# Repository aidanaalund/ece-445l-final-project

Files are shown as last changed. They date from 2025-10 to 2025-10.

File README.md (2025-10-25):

# ECE 445L Final Project

This final project is titled 'Magic Wand'. The user's hand is tracked with a sensor and the fans in the tubes will make a ping pong ball float to match the user's hand distance. Won professor's vote at the Spring 2025 Embedded Systems competition.

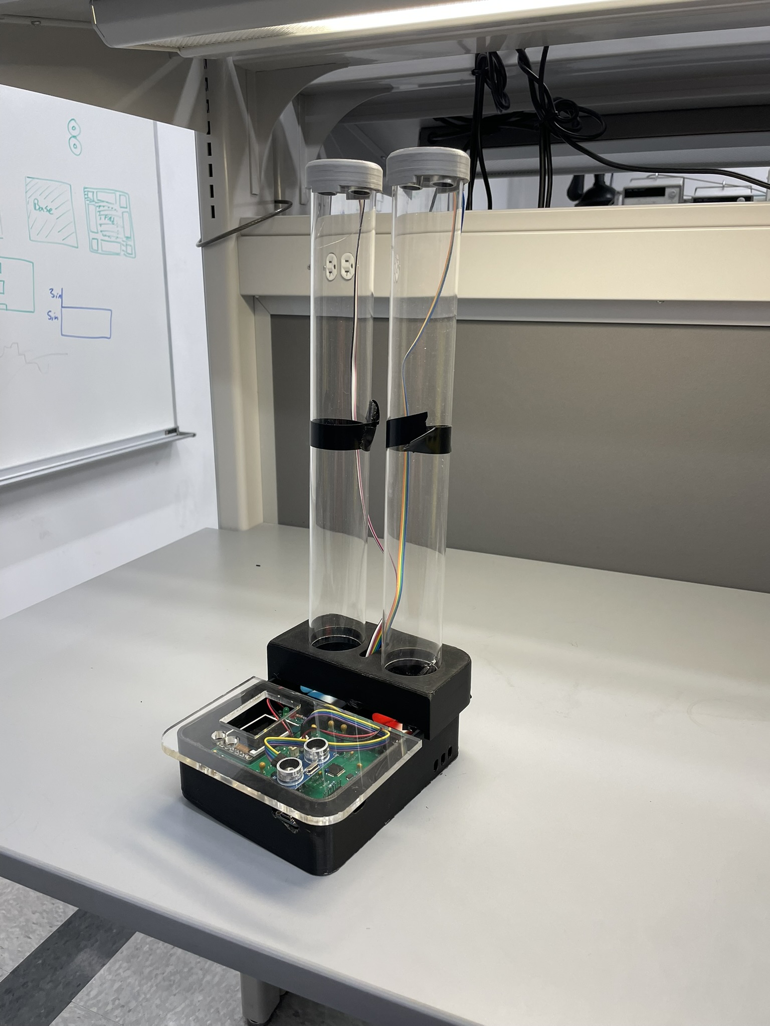
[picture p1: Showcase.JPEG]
Entire system including packaging and sensors connected
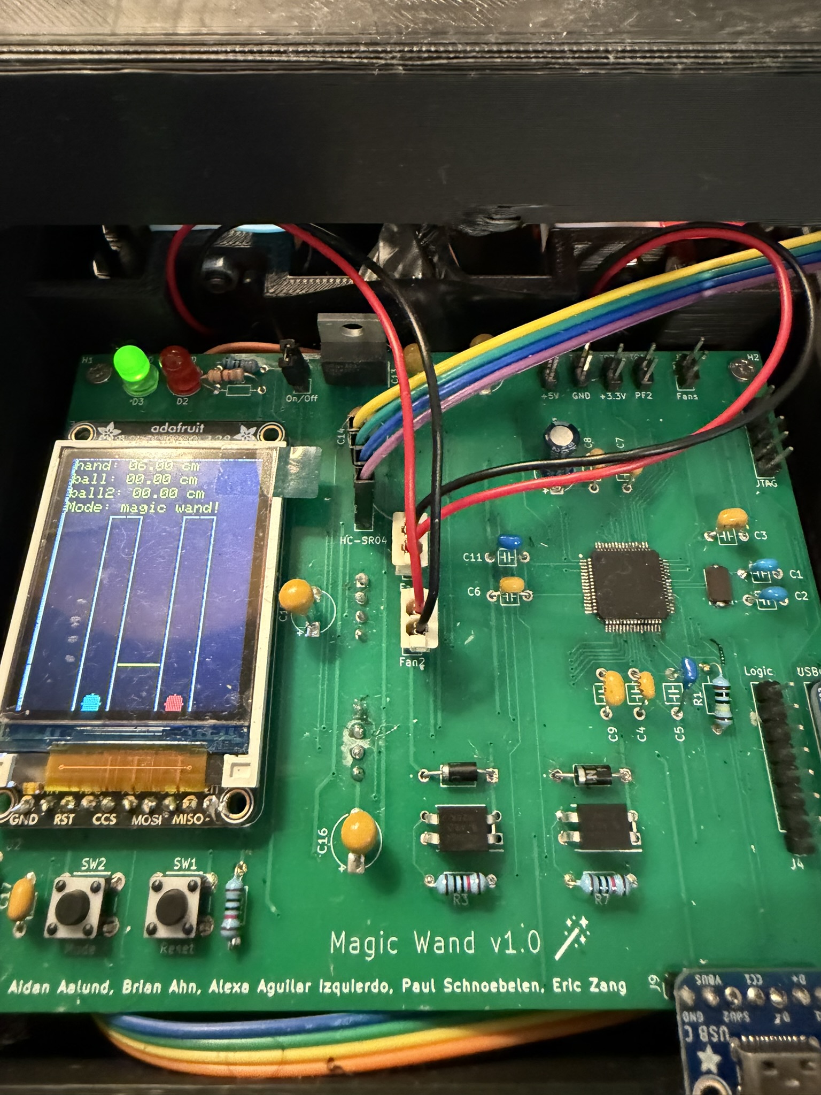
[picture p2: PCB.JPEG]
PCB featuring the TM4C microcontroller, all hand soldered.
 

## 0 Repository Structure

The typical explanation for the repo structure. Lab specific instructions can be
found further below.

### 0.1 HW

The `hw` folder should contain your schematic and board files for your PCB or
circuits. In labs 1-5 and 10, you will be creating schematics for your circuit
in KiCad. 

### 0.2 SW

The `sw` folder should contain your application firmware and software written
for the lab. The `sw/inc` folder contains firmware drivers written for you by
Professor Valvano. Feel free to write your own (in fact, in some labs, you may
be required to write your own).

You can place any other source files in the `sw` folder. TAs will look at the
files you create and/or modify for software quality and for running your
project.

### 0.3 Resources

A couple files are provided in the Resources folder so you don't have to keep
searching for that one TI document. Some of them are immediately useful, like
the TM4C datasheet. Others may be useful for your final project, like the
TM4C_System_Design_Guidelines page.

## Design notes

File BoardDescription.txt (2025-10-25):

Our board will help us create a fun visual effect with a tube, fan, and ping pong ball in the tube. 
The PCB will contain connections for 2 HC-SR40 Ultrasonic distance sensors and a motor that can be interfaced with PWM (circuit similar to Lab 2/3/4).
The user will use their hand (or a magic wand we give them) to point at a spot on the tube, read by one of the distance sensors.
Using a second distance sensor to read the ping pong ball's position, we will move the ping pong ball in the tube to match the other sensor's position with a PI loop.
This will give the appearance that the ball 'magically' follows the user's wand/hand.
There will also be additional modes for the user to switch between with an onboard pushbutton such as an off state, hover, and oscillate (hopefully!).

NOTE: the board will be powered by a USB-C 5V connection using this breakout board:
https://www.adafruit.com/product/4090

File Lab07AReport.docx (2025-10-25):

Name: __Aidan Aalund, Alexa Aguilar Izquierdo, Paul Schnoebelen, Eric Zang, Brian Ahn____

EID: __ ala4225, aa88886, pds2239, etz87, ba26422_____

Semester: Fall 2025

Course: ECE445L

A) Objectives:

1. In a few sentences, describe the purpose of the lab:

To learn about embedded system design, particularly when crafting the bill of materials and schematic of the embedded system.

B) Hardware Design Deliverables:

1. Deliverable 1: Using KiCad, create a schematic for your design. Include a screenshot in the space below.

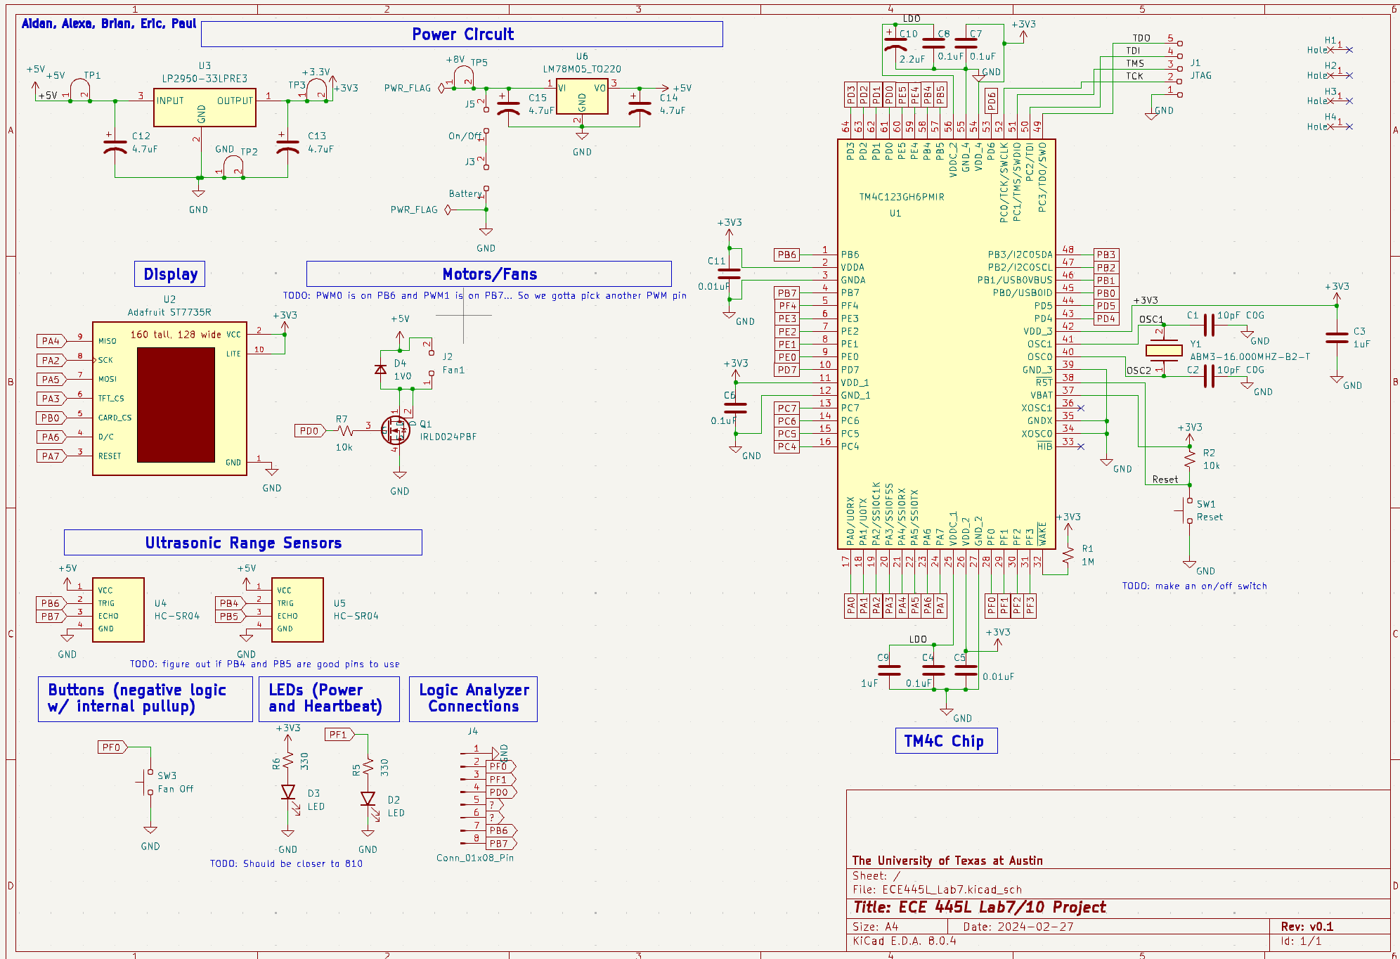
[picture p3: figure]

2. Deliverable 2: Using KiCad, create a Layout for your design. Include a screenshot in the space below.

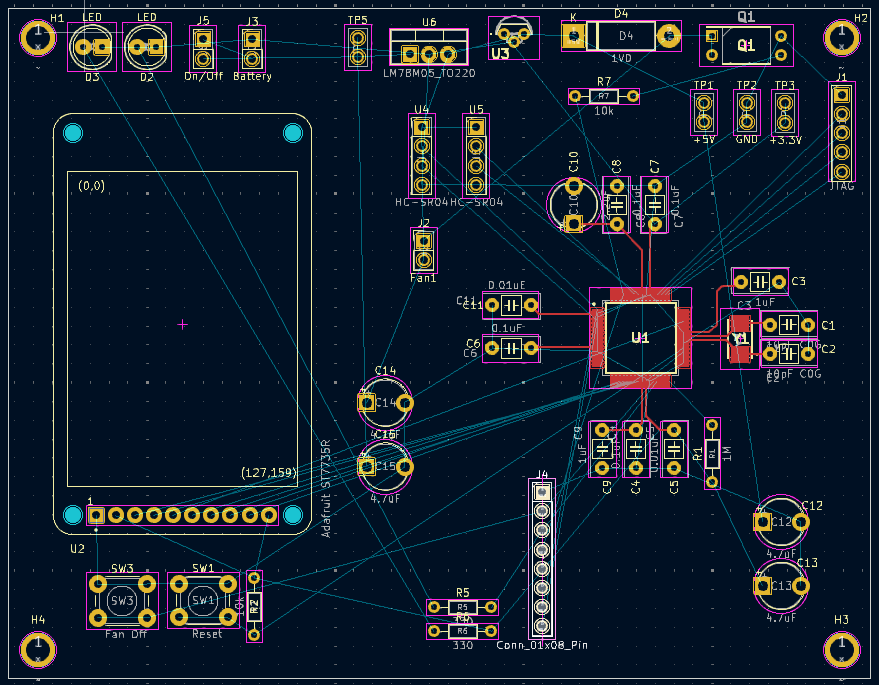
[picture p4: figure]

C) Software Design Deliverables:

I have pushed my project to GitHub for grading (Yes/No): Yes

1. Deliverable 3: System design diagram of the modules created.

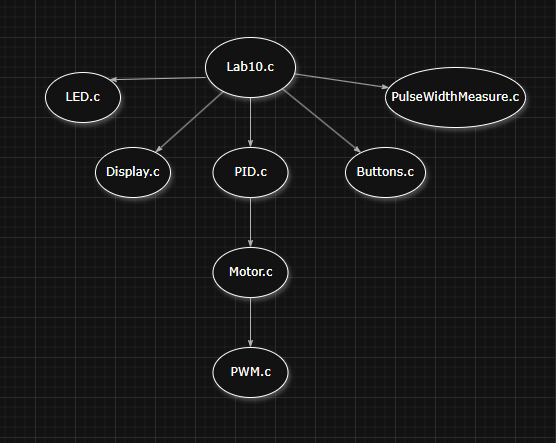
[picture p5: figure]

D) Deliverables:

1. Deliverable 4: Total cost estimate

I have updated the bill of materials (Yes/No): Yes

Out of pocket costs: $56.99

Adjusted competition costs: $42.44

2. Deliverable 5: Estimated current usage

TM4C: 45mA

Display: 50mA

Motors: 2(300mA)

Motion Sensor: 3(15mA)

Voltage Regulator: 100mA

LEDs: 2mA + 1mA

Total Current Usage: 45m + 2(300m) + 3(15m) + 100m + 2m + 1m + 50mA

= 0.843A

3. Deliverable 6 (5pt EC): TIW Training

Alexa got 3D printing training, Aidan is in progress.

4. Deliverable 7 (10pt EC): Discrete IC usage

Yes, check the layout.

5. Deliverable 8 (10pt EC): Characterization of the system

E) Analysis and Discussion Questions:

1. How did you debug your system? How intrusive was it?

We debugged our system through unit tests (‘test’ mains in each C file). In these unit tests we did a mix of intrusive breakpoint debugging and unintrusive functional debugging. For the PWM of the motor, we debugged the duty cycle and frequency with a logic analyzer (minimally intrusive). Once a module was unit tested, we performed integration tests by adding it to the Lab10.c main file and checking to see if behavior was the same as unit tests.

2. What’s the difference between unit testing, integration testing, and functional testing?

Unit testing is testing a single component of the system in isolation, whereas integration tests check if the module can function in the system with other components active. Functional testing is to see if the system works as per the requirements document.

Lab 7A report ECE445L

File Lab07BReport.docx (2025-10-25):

Name: __Aidan Aalund, Alexa Aguilar Izquierdo, Paul Schnoebelen, Eric Zang, Brian Ahn____

EID: __ ala4225, aa88886, pds2239, etz87, ba26422_____

Semester: Fall 2024

Course: ECE445L

A) Objectives:

1. In a few sentences, describe the purpose of the lab.

The purpose of this lab is to learn about the layout of an embedded system in the context of embedded system design. Examples include placement of bypass capacitors, routing power/digital/analog signals, and use of integrated circuits.

B) Hardware Design Deliverables:

1. Deliverable 1: Using KiCad, create a schematic for your design. Include a screenshot in the space below.

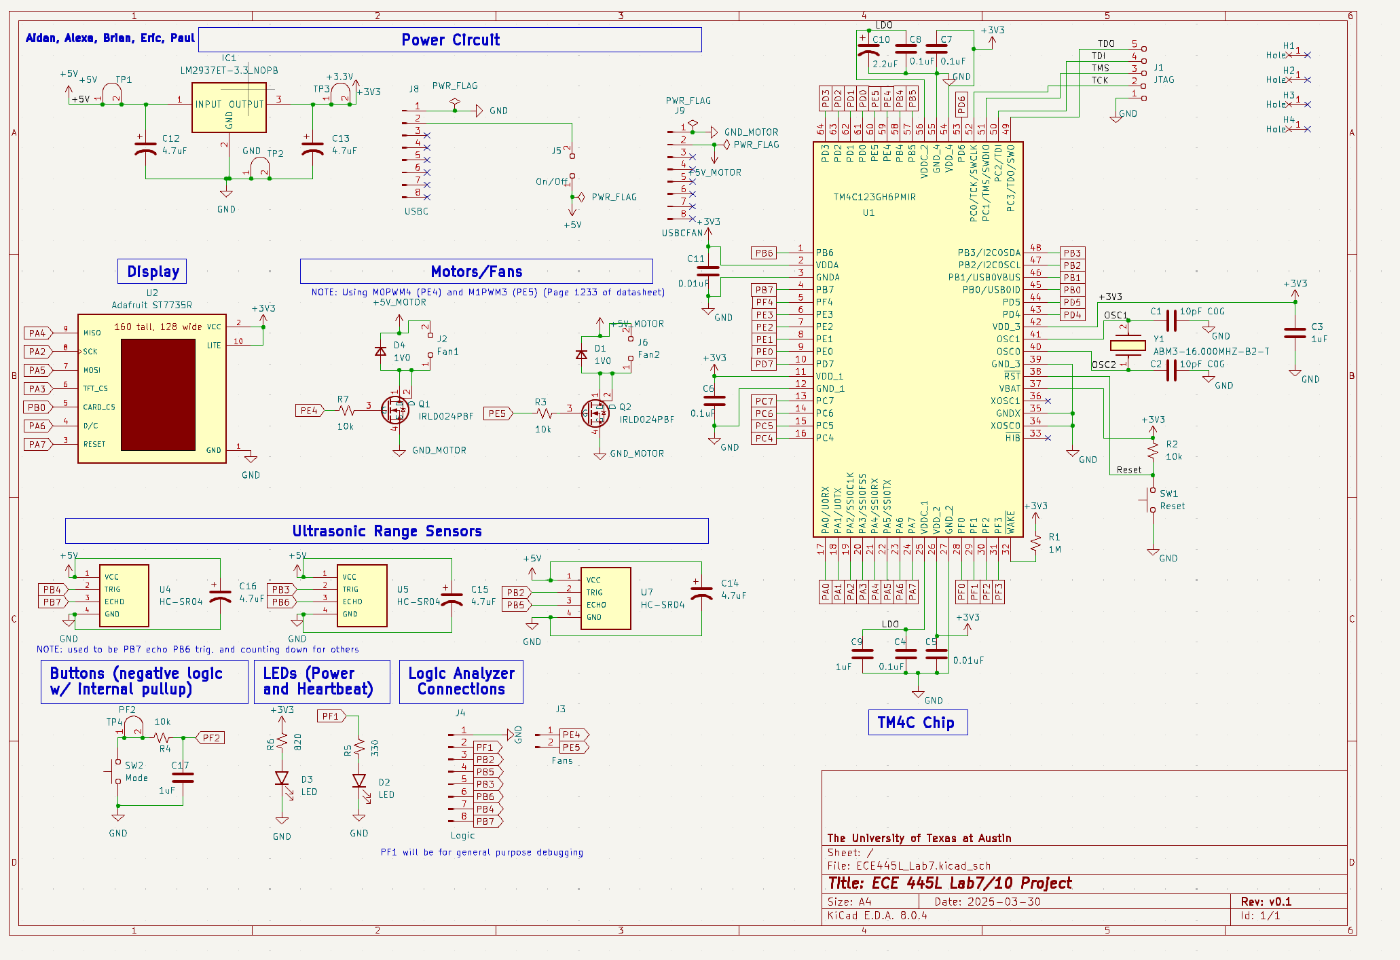
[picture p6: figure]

2. Deliverable 2: Using KiCad, create a Layout for your design. Include a screenshot in the space below.

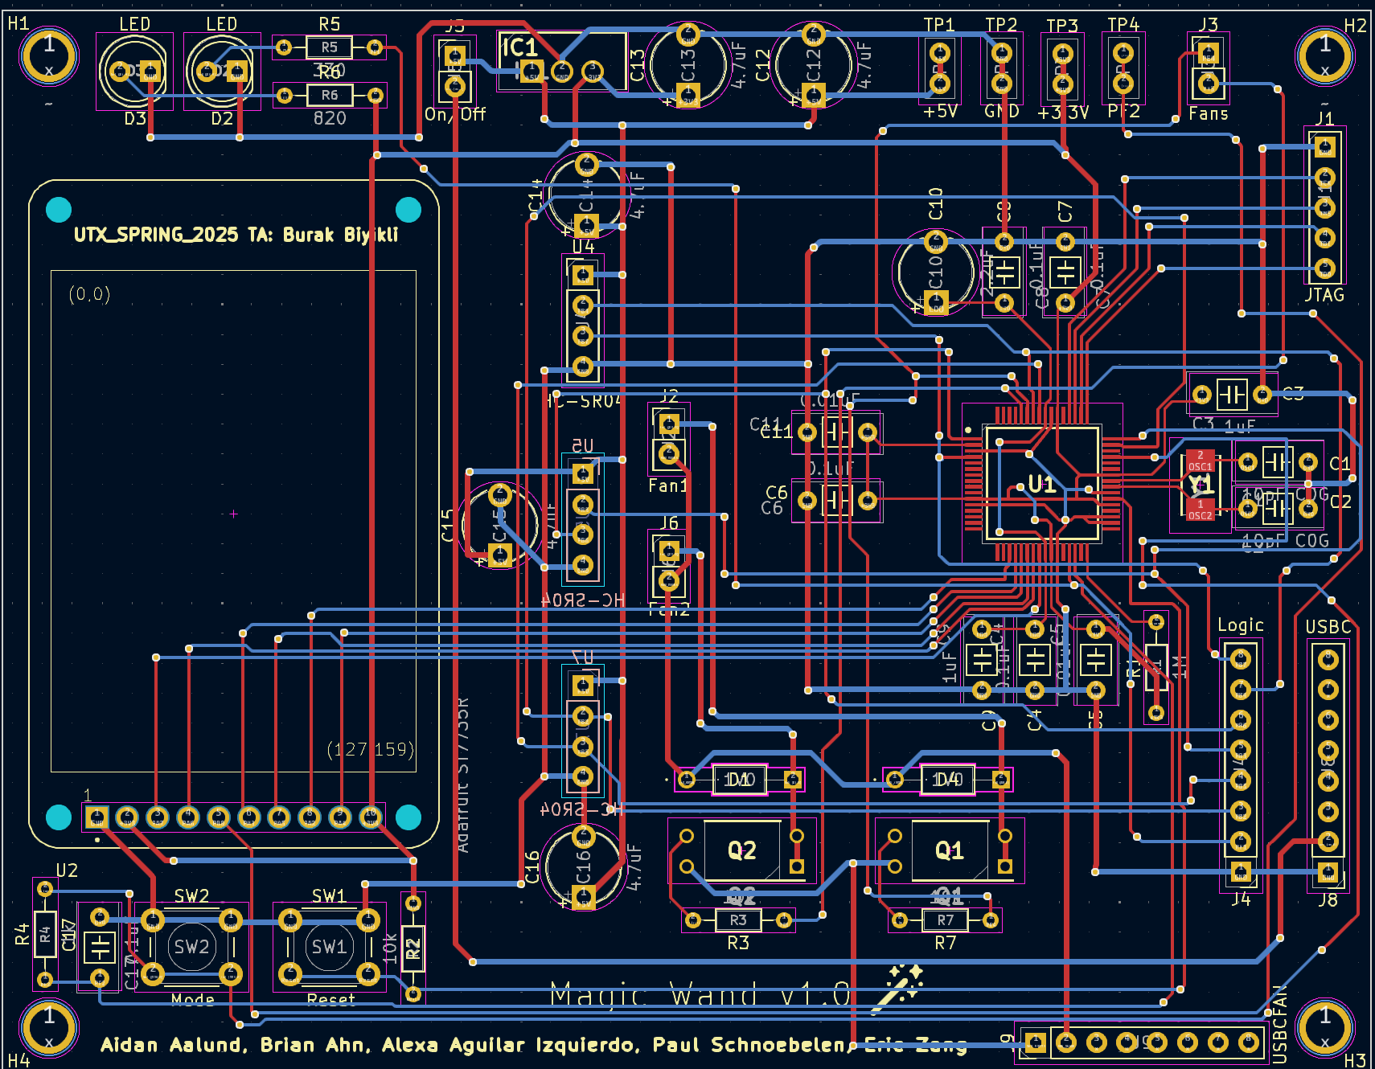
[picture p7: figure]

C) Software Design Deliverables:

1. I have pushed my project to GitHub for grading (Yes/No): Yes
2. Deliverable 3: System design diagram of the modules created.


D) General Deliverables:

1. Deliverable 4: Total cost estimate

I have updated the bill of materials (Yes/No): Yes

Out of pocket costs: $60.66

Adjusted competition costs: $44.94

2. Deliverable 5: Description of tests added for lab 7B

Integration tests were added for all 3 sensors running at once with the motor.

3. Deliverable 6 (10pt EC): Discrete IC usage

Yes, check the layout.

4. Deliverable 7 (10pt EC): Characterization of the system

E) Analysis and Discussion Questions:

1. What is the required naming scheme of the PCB submitted to us for review and ordering?

EIDs of all team members with underscores in between.

Lab 7B report ECE445L

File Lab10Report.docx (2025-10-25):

Name: __Aidan Aalund, Alexa Aguilar Izquierdo, Paul Schnoebelen, Eric Zang, Brian Ahn____

EID: __ ala4225, aa88886, pds2239, etz87, ba26422_____

Semester: Spring 2025

Course: ECE445L

A) Objectives:

1. In a few sentences, describe the purpose of the lab and the features of your project.

The purpose of the lab is to finish the design of an embedded system for real-world use. Our project’s features include 2 spinning fans that control the height of 2 ping-pong balls, a range sensor that takes the user’s hand position as input to control the height, a display, user buttons, and an enclosure.

B) Hardware Design Deliverables:

1. N/A

C) Software Design Deliverables:

1. I have pushed my project to GitHub for grading (Yes/No): Yes
2. Deliverable 1: System design diagram of the modules created.

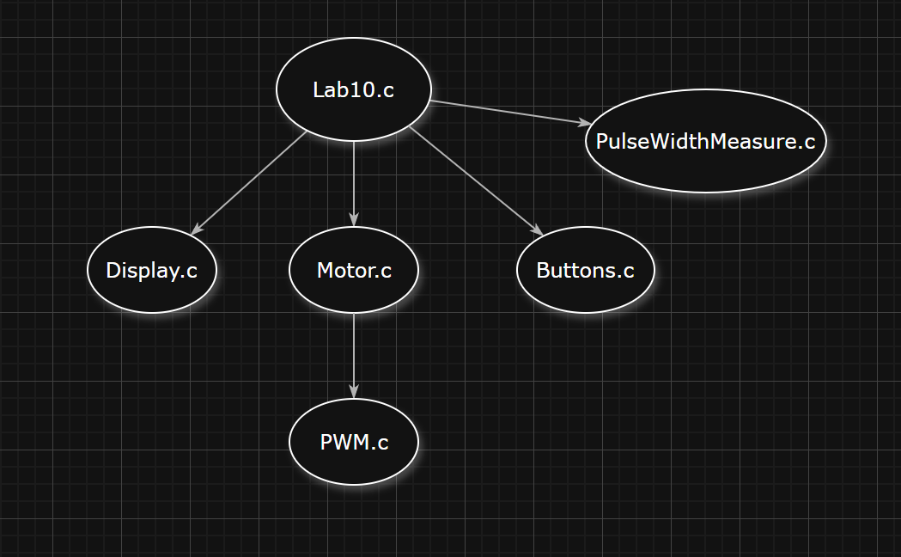
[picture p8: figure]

D) General Deliverables:

1. Deliverable 2: Software Tests

We created different software modes to test our system. The first mode was called ‘hover’, which simply aimed to bring the ping-pong balls to the middle of the tube. This let us see the behavior of our control loop in a steady state without a changing target. After that, we created an ‘oscillation’ mode that slowly moved the ping-pong balls up and down the tube. Once both of these modes were tested, we created the ‘magic’ mode that lets the user’s hand control the position of the ball, intended as the main mode for the final product.

2. Deliverable 3: Hardware Tests

We first powered the system from a power supply rather than a USB-C breakout board. Once we verified the power light LED and the display turned on, we ran the simple assembly program provided in ValvanoWare in debug mode to verify the TM4C was soldered correctly and the JTAG interface worked. After that we ran a simple test program that showed the readouts of the ultrasonic range sensors. To verify the fans worked, we used a function generator to give them a PWM signal independent of our TM4C.

3. Deliverable 4: Power consumption

Current consumption of motors circuit at max PWM: 733mA

Current consumption of sensors and TM4C: 58mA

Total power consumption: 5V*733mA + 3.3V*58mA= 3.86W

4. Deliverable 5 (10pt EC): Characterization of the system

E) Analysis and Discussion Questions:

1. N/A

Lab 10 report ECE445L

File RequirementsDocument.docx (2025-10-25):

## Project Requirements Document:

1) Overview
  a) Objectives: Why are we doing this project? What is the purpose?

To demonstrate PI control and create a fun visual effect.

  b) Interactions with Existing Systems: Include this if you are connecting to another board

N/A

  c) Terminology: Define domain specific terms used in the document.

PID Control: A method of feedback control to manage systems using 3 different gains: proportional, integral, and derivative.

2) Functional Description
  a) Functionality: What will the system do precisely?

The system will consist of 1-3 clear tubes that contain a ping-pong ball, a fan at the bottom, and an ultrasonic range sensor at the top. The ultrasonic range sensor will detect the ping-pong ball’s displacement and give it to the TM4C through a digital pin. The pulse width the sensor gives this digital pin is proportional to the displacement of the ball. This information is compared to a desired displacement and a PID loop is used to determine how fast the fan should spin to get the ping-pong ball to the desired displacement.

  b) Performance: Define the measures and describe how they will be determined.

Define the measures and describe how they will be determined.

The measures we will take for the system will be how quickly we can change the ball's position by toggling a pin whenever the interrupt is triggered. We want to optimize the PID loop to reduce as much latency as possible. We will measure the noise of the range sensor to determine the best way to optimize the PID loop. We will also include voltage test points on the PCB for the motor, power source, TM4C voltage, and ground. The PCB will also include power and heartbeat LEDs, and an 8-pin logic analyzer.

  c) Usability: Describe the interfaces. Be quantitative if possible

The interfaces we will have are for the distance sensor, fan motor, LEDs, and display. The distance sensor will have a main function where we will request distance, and we will compute the distance and send it back in centimeters. This will probably use a timer and math. The fan motor will have a main function as well to take in the input from the distance sensor in centimeters and output a fan speed to push up ping pong ball. This will involve using PI loops and PWM driving a motor. For the display, we will have a main function that can be called to output specific information. Lastly, we will have a led interface. This will light up LEDs up to the ping pong ball.

3) Deliverables
  a) Roles and Responsibilities: Who will do what? What is the purpose?
    i) Aidan: PID loop code, soldering, schematic and layout
    ii) Alexa: 3D printing, motor
    iii) Eric: PWM driver code
    iv) Paul: Range sensor code, display code, and help with PCB layout
    v) Brian: Displays, schematic and layout

The purpose of the system is to create an interesting visual and interactive effect.

  b) Reports: Simply state the reports for Labs 7, 8, and 10 will be written

The team will write reports for labs 7A, 7B, and 10.

  c) Outcomes: What are the deliverables? How do we know when it is done?

Deliverables include the complete bill of materials, requirements document, datasheet, schematic, PCB layout, and low-level driver code. We will be done when all the features in the requirements document are complete.

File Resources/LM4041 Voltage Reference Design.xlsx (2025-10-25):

Goal: design a shunt reference circuit
Jonathan Valvano, EE445L
Desired Vz | 1.5 | volts | 1) pick a desired reference voltage Vz (volts)
Vref | 1.233 | volts | LM4041 parameter
R1 | 47 | kohm | 2) choose a standard resistance value (kohm)
best R2 | 10.17761557 | kohm
Pick R2 | 10 | kohm | 3) pick a standard value for R2 close to best R2
Actual Vref | 1.495340426 | volts | Vz=Vref(1+R2/R1)
Vs | 3.3 | volts | V supply
Rin | 2 | kohm | 4) estimate input impedence on Vz (e.g., to DAC)
Iz | 0.08 | mA | LM4041 parameter
Iref | 0.02623404255 | mA | Vz/(R1+R2), Ohms Law, current through R1,R2
IL | 0.7476702128 | mA | Vz/Rin, Ohms Law, current through Rin
I total | 0.8539042553 | mA | Iz+Iref+IL
max Rs | 2.113421456 | kohm | (Vs-Vz)/Itotal
 |  |  | 5) choose Rs less than max Rs

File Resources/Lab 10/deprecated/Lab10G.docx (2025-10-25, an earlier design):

This laboratory assignment accompanies the book, Embedded Systems: Real-Time Interfacing to ARM Cortex M Microcontrollers, ISBN-13: 978-1463590154 (https://www.amazon.com/Embedded-Systems-Real-Time-Interfacing-Microcontrollers/dp/1463590156), by Jonathan W. Valvano, copyright © 2021.

## Goals

- To interface a DC motor using PWM so software can adjust delivered power
- To interface a tachometer so the software can measure speed
- To implement the data acquisition with input capture interrupts
- To implement the digital controller processing with periodic interrupts
- To study the behavior of the system as parameters to the proportional-integral (PI) controller are adjusted

## Responsibilities:

- Student 1: Motor and interface hardware and PWM output
- Student 2: Tach hardware and input capture measurement of speed
- Student 3: Digital Controller
- Student 4a: User interface (Blynk, UART, LCD)
- Student 4b: User interface UART0 to PC, command interpreter
- ALL: Tinker with variations of the PI control loop

Team Size: 4

Figure 10.1: Lab 10G Block Diagram.

## Review

- Valvano Section 6.1.3 about using input capture to measure period
- Valvano Section 6.3 about generating PWM outputs
- Valvano Section 6.5 about interfacing a DC motor with a IRLD024 or IRLD120
- IRLD120 data sheet (https://www.dropbox.com/s/ulcq0selng2aqfx/IRLD120.pdf?dl=1)
- IRLD024 data sheet (https://www.dropbox.com/s/u49pvrn8jz70aru/sihld24.pdf?dl=1)
- Pololu motor https://www.pololu.com/product/3675
- Valvano Section 6.6 about integral control (you will need to add proportional control (https://www.et.byu.edu/~tom/classes/436/ClassNotes/Class07-PI.pdf))

## Starter files

- PWM_4C123 PeriodMeasure_4C123
- PeriodicTimer0AInts_4C123
- Python starter 4/13/22 https://www.dropbox.com/s/xow3r4eumwcakj0/Python.zip?dl=1
- Lab 10G Eagle starter Schematic
- (https://www.dropbox.com/s/pyssg7koidkfg54/Lab10_Starter.sch?dl=1)EE445M http://users.ece.utexas.edu/%7Evalvano/arm/MotorTestProject.zip
- EE445M https://www.dropbox.com/s/vtjc5j6hz9b15dj/SensorTestProject.zip?dl=1

## Required Hardware (hardware groups building with discrete parts)

EK-TM4C123GXL https://store.ti.com/ (https://store.ti.com/ProductAccessories.aspx?ProductId=4505) $12.99

Sitronix ST7735 Color LCD http://www.adafruit.com/products/358 $19.99

Pololu item #3675 https://www.pololu.com/product/3675 $13.95

1N914B 4ns switching diode

Two 10k resistors

IRLD024 or IRLD120 MOSFET

## Background

The advantages of DC motors include low cost, high speed, and high torque. However, they need sensors and closed-loop controllers in order to operate them with predictable responses. Applications of DC motors include electric cars, robotics, industrial machines (pumps, drills, mills, and lathes), consumer products (blender, washing machine, and AC/heaters) and medical devices (pumps). In this lab, you will spin a brushed DC motor (Figure 10.2) at a constant speed using a proportional-integral (PI) controller. The user interface will allow the operator to increase or decrease the desired speed. A tachometer will be used to measure the motor speed. A background periodic interrupt will execute the three steps of a digital controller.

1. Calculate error as the difference between actual and desired speed
2. Execute a control equation to determine the next output
3. Adjust the power to the actuator in an attempt to drive the error to zero

The software will set the power delivered to the motor using pulse-width-modulation (PWM). The essence of an integral controller is the amount you add to the power is linearly related to the error. If the motor is spinning much too slowly, you will increase power a lot. If the motor is spinning just a little bit too slowly, you will increase power a little bit. If the motor is spinning much too quickly, you will decrease power a lot. If the motor is spinning just a little bit too quickly, you will decrease power a little bit. The input capture input and the PWM output must be written at a low level, like the book, without calling TivaWare driver code. No TivaWare code is allowed.

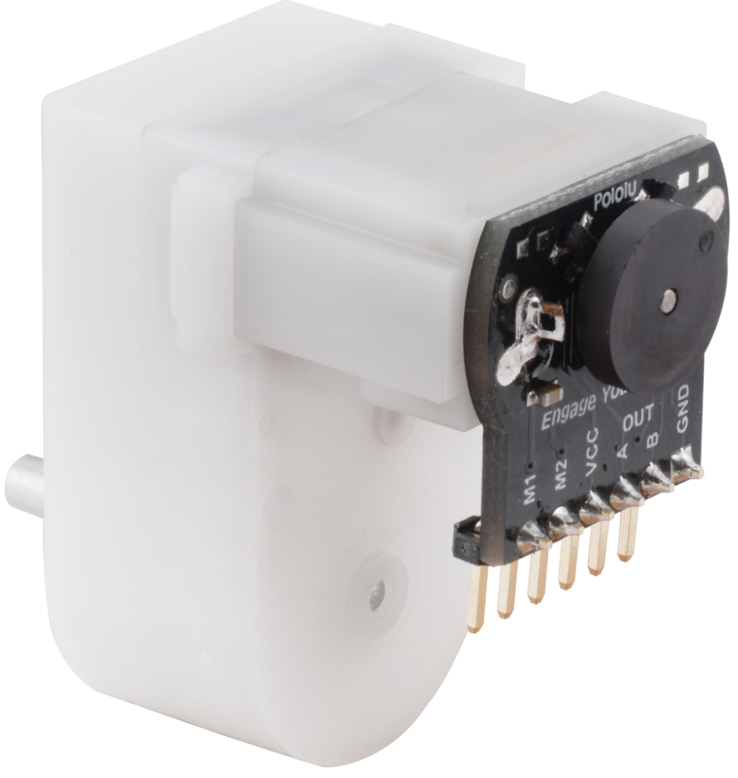
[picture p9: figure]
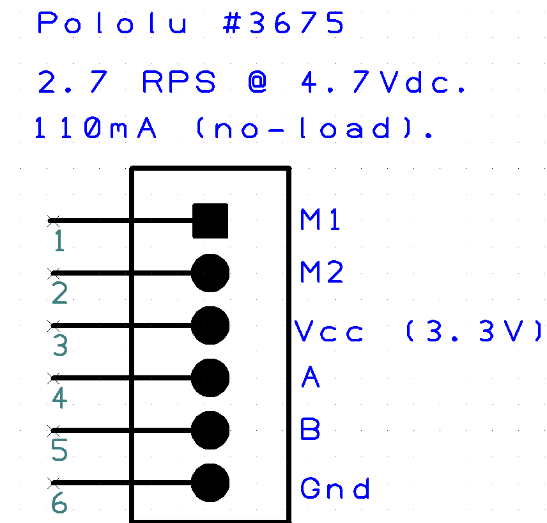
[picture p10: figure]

Figure 10.2. Hardware groups use Pololu item #3675. M1 and M2 connect to the DC motor and the other four wires are the tachometer. Do not ground A or B, they are outputs.

Figure 10.3 shows a possible data flow graph.

Figure 10.3. Option 1) Lab 10G data flow graph.

Student 4 creates a mechanism to visualize and control the system

Option 1) Student 4 implements Blynk

Option 2) Student 4 implements UART0/USB/PC/Python

Figure 10.4 shows a possible call graph.

Figure 10.4. Lab 10G call graph.

Option 2) replace Blynk with UART0/USB/PC/Python

## Student 1 Motor Interface

Choose Port-B[6] on the TM4C123 for the PWM output. The LM4F120 does not have hardware PWM. So, if you have an LM4F120 LaunchPad you will need to use one of the timers to create the PWM output. Use a 10k resistor into the gate to reduce transients. Use a 1N914 (any fast diode is ok) to remove back EMF caused by the V=L*dI/dt across the motor (see Figure 10.5). Connect M2 to +5V and use the IRLD024/IRLD120 to sink current from the M1 to ground. Refer to IRLD024/IRD120 interface in aLec42_DC_Motors.pptx (https://www.dropbox.com/s/ez9kxdaawj3j3xy/aLec42_DC_Motors.pptx?dl=1).

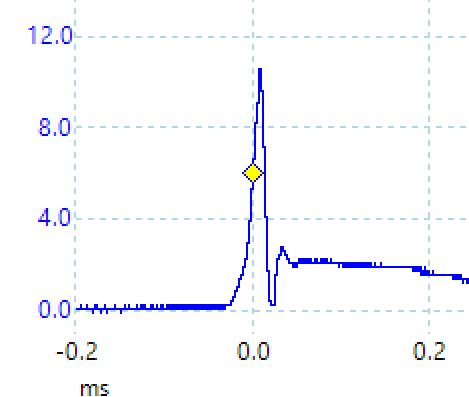
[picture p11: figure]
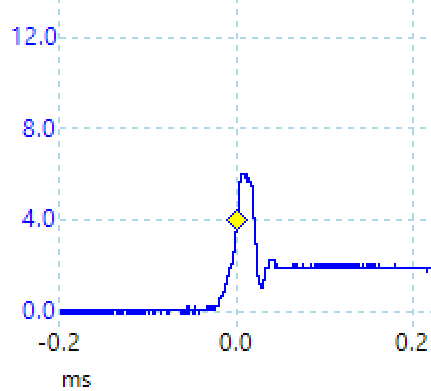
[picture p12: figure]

Figure 10.5. Voltage from drain to source (motor – to ground) when current is removed. The left response was measured without the 1N914 shunt diode and the response on the right was measured with the 1N914 shunt diode. The steady state 2-3V output after 0.05ms occurred because the pin was floating at the point in time

In order to choose a PWM period you will need to know the time constant of your motor. Figure 10.6 is measured speed as a function of time as PWM is increased from 25 to 50%. You can estimated the time constant of this motor to be 50 ms. Therefore if the PWM period is 1ms, the motor will only respond to the average power (duty cycle), and not to the individual high and low signals of the interface.

Figure 10.6. Step response of the DC motor used to estimate the time constant. Expect your measured speeds to be slower (this data was collected at 7.2V.)

## Student 2 Tachometer Interface

To interface the tachometer, connect VCC to 3.3V and GND to GND. Choose a TM4C123 pin that supports input capture interrupts. Use a 10k pullup to 3.3V for the tachometer output (A or B). You can use either A or B. You could interface both A and B to input capture if you wished to reduce the time to measure speed or if you wished to measure direction. There are 12 tachometer pulses per rotation (https://www.pololu.com/product/3542). Figure 10.7 shows the tachometer output of 973.4 Hz, ~~which is~~ ~~60*~~~~973.4/360 rp~~~~m~~ ~~=~~ ~~162~~ ~~rp~~~~m~~. If the motor spins from 0 to 162 RPM, then choose a fixed-point resolution of 0.1 or 0.01 RPM. Choose a resolution based on the ability of the tachometer to measure speed at 100 RPM.

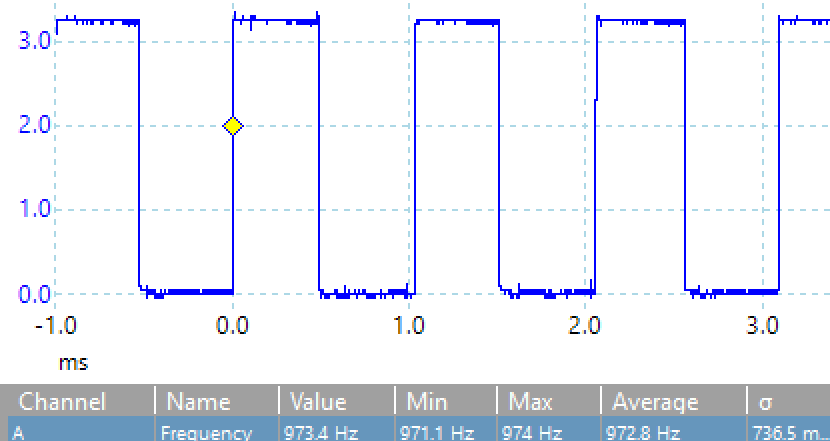
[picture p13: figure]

Figure 10.7. Tachometer output at full speed.

The tachometer interface may require filtering to improve SNR. However, be careful to minimize time delay. Time delays in the digital controller will cause the system to be unstable. For any digital filter measure the step response. A simple measure of filter delay is to make input go from …x,x,x,x,y,y,y,y… and determine many samples it takes for the output of the filter to reach x+(y-x)e⁻¹. For example, the delay of a 3-wide median filter is 1 sample.

You will need a separate periodic timer interrupt to determine if the motor is spinning too slow to be accurate or not spinning at all.

## Student 3 Digital Controller Design

A closed loop feedback is required because not all motors are created equal. In Figure 10.8 we see the results from 8 different motors (the ones from the lab board, not this one however). One of the first steps in designing a digital controller is to make an estimate of motor speed in RPM versus PWM duty cycle. This curve will help estimate the range of speeds that your controller will be able to manage. In other words, what speeds correspond to duty cycles from 25 to 75%? Note: this response is highly dependent on friction. We expect the usable range to be around 50 to 120 RPM, but your motor may be different. You are free to control speed in rps or RPM as long as the fixed point resolution matches the tachometer error. The design progression is

1. Incremental (stable but slow)
2. Integral (stable, a little faster)
3. Proportional-integral (may be unstable, fast)

## Student 4 Blynk Control Interface or UART/Python Interface

Convert the Lab 4D Blynk code to provide variables to the PI control loop and display the key output values of the motor controller on the LCD. See figures 10.8, 10.12-10.15 below.

## Requirements Document

1. Overview

1.1. Objectives: Why are we doing this project? What is the purpose?

The objectives of this project are to design, build and test a brushed DC motor controller. The motor should spin at a constant speed and the operator can specify the desired set point. Educationally, students are learning how to interface a DC motor, how to measure speed using input capture, and how to implement a digital controller running in the background.

1.2. Process: How will the project be developed?

The project will be developed using the TM4C LaunchPad. The user will use switches or the UART to specify the desired speed of the motor as well as the “K” terms for the Proportional and Integral components of the PI controller. The system will be built on a solderless breadboard and run on the usual USB power. A hardware/software interface will be designed that allows software to control the DC motor. There will be at four hardware/software modules: motor controller output, tachometer input, digital controller, and user interface with switches, UART and LCD. The process will be to design and test each module independently from the other modules. After each module is tested, the system will be built and tested.

1.3. Roles and Responsibilities: Who will do what? Who are the clients?

EE445L students are the engineers and the TA is the client. Student 1 will design build and test the motor controller output. Student 2 will design build and test the tachometer input. Student 3 will design build and test the digital controller. Student 4 will design build and test the user interface with switches. All students will work performance measurements and tuning the controller. (note to students: you are expected to make minor modifications to this document in order to clarify exactly what you plan to build. Students are allowed to divide responsibilities of the project however they wish, but, at the time of demonstration, both students are expected to understand all aspects of the design.)

1.4. Interactions with Existing Systems: How will it fit in?

The system will use the microcontroller board, a solderless breadboard, and the DC motor shown above in Figure 10.2. The wiring connector for the DC motor is described in aLec42_DC_Motors.pptx (https://www.dropbox.com/s/ez9kxdaawj3j3xy/aLec42_DC_Motors.pptx?dl=1).

1.5. Terminology: Define terms used in the document.

For the terms Proportional-Integral (PI) controller, PWM, board support package, back EMF, torque, time constant, and hysteresis, see textbook for definitions.

1.6. Security: How will intellectual property be managed?

The system may include software from TivaWare and from the book. No software written for this project may be transmitted, viewed, or communicated with any other EE445L student past, present, or future (other than the lab partner of course). It is the responsibility of each team to keep its EE445L lab solutions secure.

2. Function Description

2.1. Functionality: What will the system do precisely?

The palette for the Blynk App (Fig 10.8) will have the following 8 virtual pin components:

- Slider to control the desired motor speed
- Two sliders to control the “K” multiplier/divider for the Proportional term
- Two sliders to control the “K” multiplier/divider for the Integral term
- RPS Value display
- PWM Duty Cycle Control Value (U)
- PI Error Value (E)
- Optional: Proportional and Integral Term values

Remember to delete the Widgets from Lab 4 so that you don’t have to buy new tokens for this Lab.

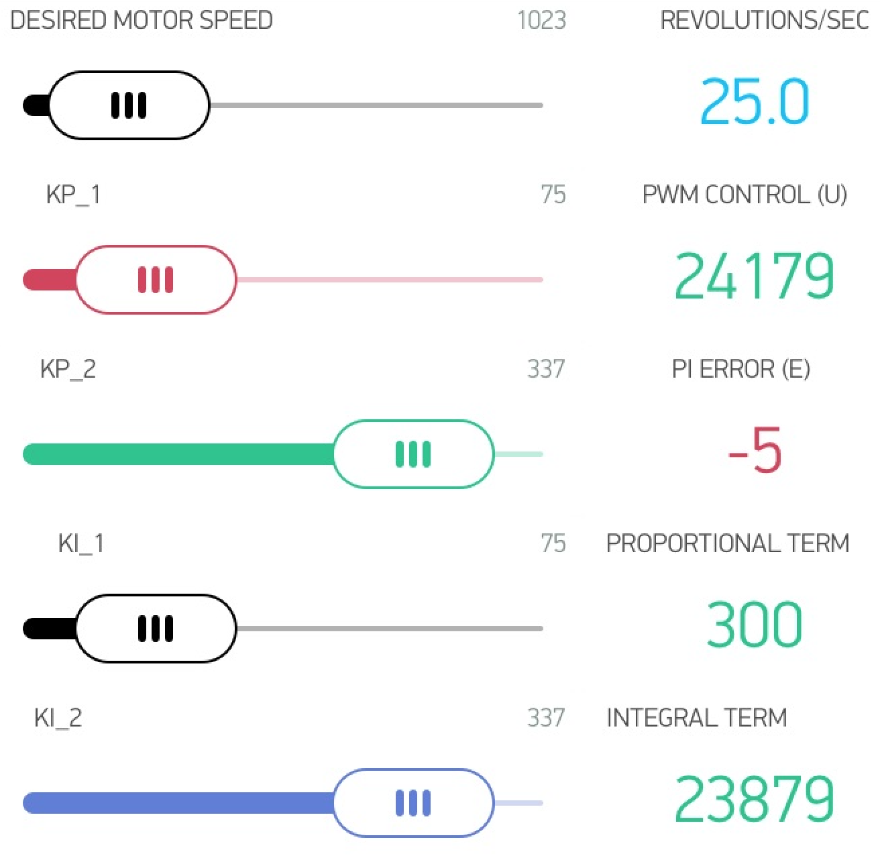
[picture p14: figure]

Figure 10.8 Blynk App palette (feel free to remove the Motor RPS so you’ll not have to buy tokens) Feel free to make this user interface however you wish. You may also have to delete the Lab 4 Blynk app

The PI control equation should be in this form:

MotorSpeed = rps/40; // Set the Motor Speed

P = (Kp1 * E)/Kp2; // Proportional term

if(P < 300) P = 300; // Minimum PWM output = 300

if(P >39900) P = 39900; // Maximum PWM output = 39900

I = I + (Ki1 * E)/Ki2; // SUM(KiDt)

if(I < 300) I = 300; // Minimum PWM output = 300

if(I >39900) I = 39900; // Maximum PWM output = 39900

U = P + I; // Calculate the actuator value

if(U < 300) U=300; // Minimum PWM output

if(U >39900) U=39900; // 3000 to 39900

PWM0A_Duty(U); // Send to PWM

The motor speed should start out at zero RPS. Once the desired motor speed slider is adjusted the motor should start. (Note to students: feel free to change how the set point is established, and feel free to increase or decrease the maximum speed in accordance to how it actually works.)

Both the desired and actual speeds should be plotted on the color LCD as a function of time similar to Figure 10.11 The actual speed should also be graphically shown on the Blynk App. (note to students: feel free to specify exactly how the data is displayed. For example, you could but do not have to add numerical outputs).

2.2. Scope: List the phases and what will be delivered in each phase.

Phase 1 is the preparation; phase 2 is the demonstration; and phase 3 is the lab report. Details can be found in the lab manual.

2.3. Prototypes: How will intermediate progress be demonstrated?

A prototype system running on the LaunchPad and solderless breadboard will be demonstrated. Progress will be judged by the preparation, demonstration and lab report.

2.4. Performance: Define the measures and describe how they will be determined.

The system will be judged by three qualitative measures. First, the software modules must be easy to understand and well-organized. Second, the system must employ a PI controller running in the background. There should be a clear and obvious abstraction, separating the state estimator, user interface, the controller and the actuator output. Backward jumps in the ISR are not allowed. Third, all software will be judged according to style guidelines. Software must follow the style described in Section 3.3 of the book (note to students: you may edit this sentence to define a different style format). There are three quantitative measures. First, the average speed error at a desired speed of 60 RPM will be measured. The average error should be less than 5 RPM. Second, the step response is the time it takes for the new speed to hit 100 RPM after the set point is changed from 50 to 100 RPM. Third, you will measure power supply current to run the system. There is no particular need to minimize controller error, step response, or system current in this system.

2.5. Usability: Describe the interfaces. Be quantitative if possible. Describe the how the Blynk App will control the motor.

2.6. Safety: Explain any safety requirements and how they will be measured.

We expect the motor current to be less than 120 mA. Please place a current probe on the motor interface the first couple of time you run the motor to make sure you have wired it correctly. However, under heavy friction this current could be 2 times higher. Therefore, please run the motor unloaded. Connecting or disconnecting wires on the protoboard while power is applied will damage the microcontroller. Operating the circuit without a snubber diode will also damage the microcontroller.

3. Deliverables

3.1. Reports: How will the system be described?

A lab report described below is due by the due date listed in the syllabus. This report includes the final requirements document.

3.2. Audits: How will the clients evaluate progress?

The preparation is due at the beginning of the lab period on the date listed in the syllabus.

3.3. Outcomes: What are the deliverables? How do we know when it is done?

There are three deliverables: preparation, demonstration, and report. (Note to students: you should remove all notes to students in your final requirements document).

## Preparation (do this before your lab period)

1. Copy and paste the requirements document from this document. Edit it to reflect your design.
2. Edit the Lab_10G.sch (https://www.dropbox.com/sh/2lzrbx88r8cgw05/AADl2iDcrez1SNAoDAh33-Kya?dl=1) file showing the interface to the motor and to the tachometer. Make sure your TA approves the design before connecting it to the microcontroller. Include pin numbers and resistor/capacitor types and tolerances. Power the motor from the USB +5V and not +3.3V. This interface will require a 1N914 snubber diode. If do not properly connect this diode, the back EMF will destroy your microcontroller and possibly your laptop if it is connected to the TM4C board.

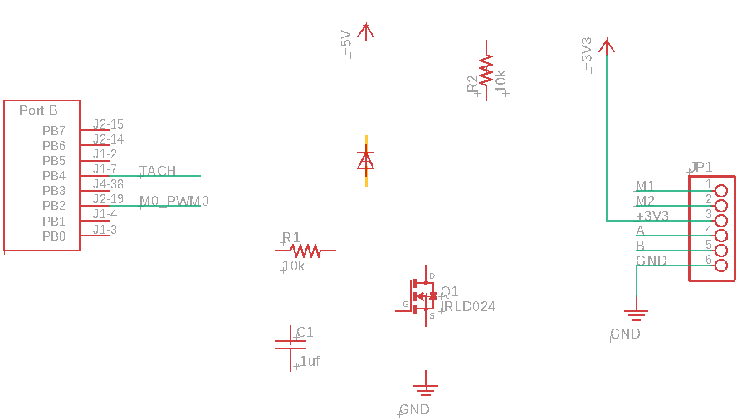
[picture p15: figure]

3. Design four software modules that implement the digital controller. A “syntax-error-free” version of the header files is required as preparation. This will be checked off by the TA at the beginning of the lab period. If you wish to see more timer and PWM examples, see the EE445M sensor board and motor board starter projects (see starter files above).

## Student 1 Procedure (do this during your lab period)

With an ohmmeter, measure the resistance of the motor coil. The very fast turn-off times of the digital transistors can easily produce large back EMF voltages, so please test the hardware before connecting it to the microcontroller. Make sure your TA checks your hardware diagram before connecting it to the microcontroller.

Build the hardware interface to the motor. However, before connecting it to the microcontroller, you must use a simple switch to simulate a PWM output of 100%. Connect a current meter in series with the motor current path. Measure the motor current at full speed (100% duty cycle). Please contact your professor or TA if this current is vastly different from 120mA. Measure also the voltage drop across the motor at full speed (100% duty cycle). Call this full speed motor voltage Vm. The voltage drop across the MOSFET VDS should be much less than 1V. Note: VDS + Vm should equal 5V.

Test the PWM output with a scope or logic analyzer before connecting it to the motor. Write software so a switch causes the PWM to cycle through 10%, 30%, 50%, 70% and 90%.

Remove the switch, connect the PWM to the motor circuit, and reconnect the current meter in series with the motor current path. Using the PWM output in open loop fashion measure the motor current at duty cycles 10%, 30%, 50%, 70% and 90%. Do this under no load. Estimate the average motor voltage as duty*Vm. Create a graph similar to Figure 10.9 below. Plot the straight line suggested by the ohmmeter measurement of motor resistance.

Figure 10.9 was measured with the Lab board motor, so expect your measurements to be different. However, the motor does not behave like a simple resistor.

Figure 10.9: The current to the Lab board DC motor is plotted versus applied voltage. Notice the DC motor does not behave like a resistor. This response will also be a function of the mechanical torque (or friction) applied to the shaft.

## Student 2 Procedure (do this during your lab period)

Build the hardware interface to the tachometer. Using a scope (real or TExaSdisplay), verify the tachometer interface generates a digital (0V and 3.3V) signal like Figure 10.7. Speed measurement must occur in the background using an input capture and periodic interrupt.

Using the PWM output in open loop fashion measure the motor speed at duty cycles 10%, 30%, 50%, 70% and 90%. Do this under no load. Estimate the average motor power as duty*Im*Vm. Create a graph similar to Figure 10.10 below.

Figure 10.10: The motor speed is plotted versus applied power on seven different motors. Power is motor voltage multiplied by motor current multiplied by PWM duty cycle. Motor speed (RPS) is tachometer frequency (Hz) divided by 4. Notice at 100 mW, these DC motors do not spin at all. Also notice the variability between these seven motors. This response will also be a function of the mechanical torque (or friction) applied to the shaft.

## Student 3 Procedure (do this during your lab period)

After you are sure the motor and tachometer interfaces are operating properly, test a simple incremental controller, see Figure 10.11. Choose a PWM period, a range of usable speeds, and a controller rate consistent with the data collected in the above two procedures.

Figure 10.11: Incremental controller. Change the +3, -3, +100, -100, 14898 constants.

Debug the integral motor controller. Consider calculating speed as a decimal fixed-point number in 0.1 or 0.01 RPM. The periodic interrupt-driven background thread will execute the digital controller, while the foreground thread initializes the system then performs human interface. An integral controller is pretty stable. If the speed oscillates wildly (all stop- full speed) then decrease the controller constant. If it is VERY slow to respond, increase the constant.

## Student 4 Procedure (do this during your lab period)

Student 4 creates a mechanism to visualize and control the system

Option 1) Student 4 implements Blynk

Option 2) Student 4 implements UART0/USB/PC/Python

Option 1) Setup the user interface that runs in the main program. See requirements document for details. Your system performance display on the LCD should be similar to Figure 10.12 through 10.15 and the YouTube video, http://youtu.be/ug-ZlOSbb4M.

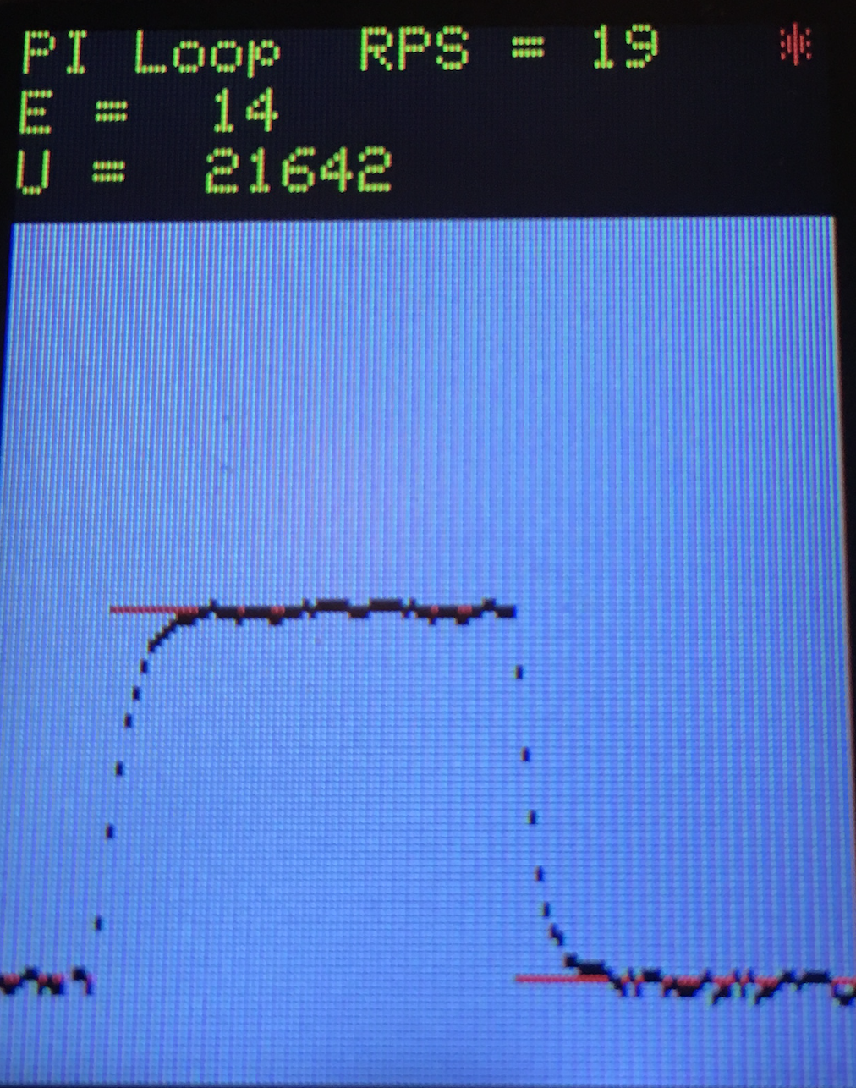
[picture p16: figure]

Figure 10.12: Measured and desired speeds are plotted versus time as the set point is increased from 20 to 50 RPS. NOTE: This is an optimally damped PI Loop (Lab board motor)

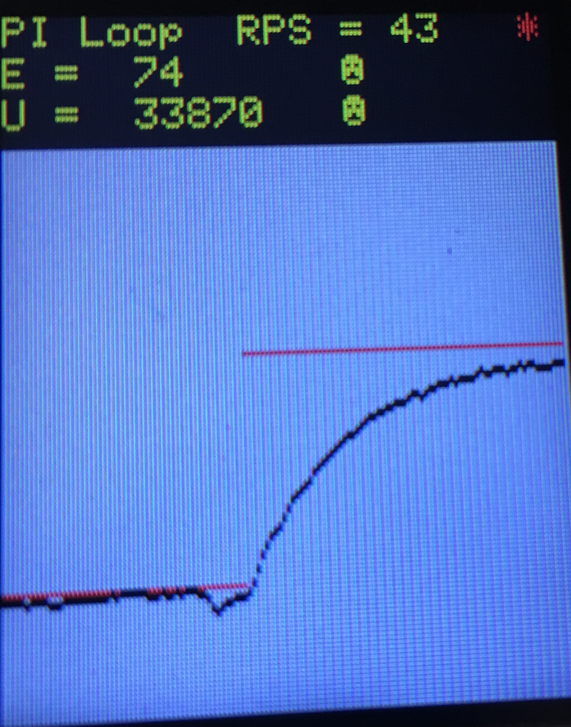
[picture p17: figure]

Figure 10.13: Over-damped PI Loop

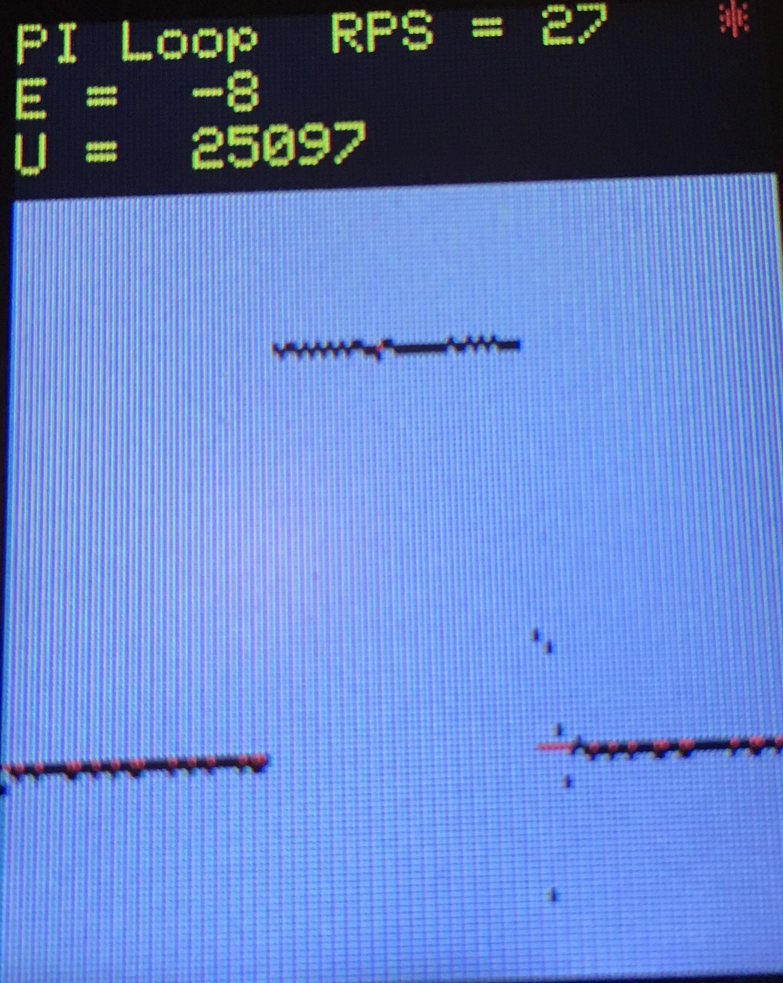
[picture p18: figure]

Figure 10.14: Under-damped PI Loop

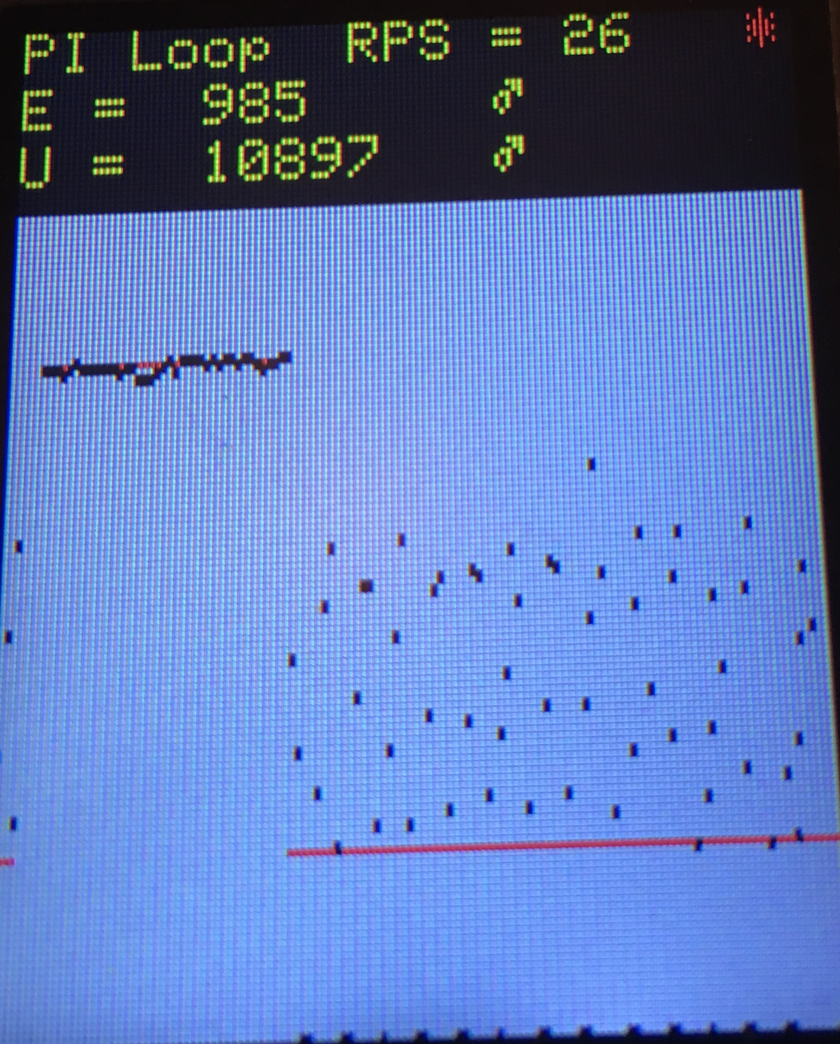
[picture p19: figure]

Figure 10.15: Unstable PI Loop

The Blynk or Python user interface should facilitate changing controllers and controller parameters. You should be able to demonstrate without recompiling.

## Student-all Procedure (do this during your lab period)

Measure the maximum time to execute each of your ISRs.

For each of the three controllers, what is the average controller error (difference between desired and actual speed)? The PI controller is optional.

For each of the three controllers, what is the approximate time it takes the speed to stabilize after the set point is increased from 40 to 90 RPM? Feel free to change these two set points has appropriate for your system. You do not need to tweak the system to minimize error or response time.

## Deliverables (exact components of the lab report)

1. Objectives (final requirements document)
4. Hardware Design (PCB Artist file)

DC motor and tachometer interfaces, showing all external components

LCD and switch interfaces, showing all external components

Include both these in a schematic

5. Software Design (upload your files as instructed by your TA)

Make sure to include units on all your software variables

Make a clear distinction between variables used for debugging and variables needed in the controller

Data flow and call graph: copy Figures 10.3 and 10.4, and edit as necessary

6. Measurement Data (underlined sections of the lab manual)

Procedure 1) Give the voltage, current, and resistance measurements. Plot motor current vs duty*Vm.

Procedure 2) Typical plot of the tachometer like Figure 10.7. Motor speed vs PWM. Plot of motor speed vs power, like Figure 10.8.

Procedure 4) We define locking as the condition when the error eventually goes to approximately zero. Four screen shots of the hardware in operation -> switching from minimum speed to

maximum speed or vice versa:

a) Normal operation – optimal response time (locking). Fig 10.11

b) Slow loop response time (locking) Fig 10.12

c) Fast loop response time (locking) Fig 10.13

d) Unstable (unable to lock) Fig. 10.14

Procedure-all) Specify the maximum time to execute once instance of the ISR. Determine the percentage time required to run all ISRs.

Procedure-all) Specify the average controller error for three controllers

Procedure-all) Specify the approximate response time for three controllers

7. Analysis and Discussion (give short 1 or two sentence answers to these questions)
a. What is torque? What are its units?
b. Draw an electrical circuit model for the DC motor coil and explain the components. Use this circuit model to explain why the current goes up when friction is applied to the shaft
c. Explain what parameters were important for choosing a motor drive interface chip (e.g., IRLD024/IRD120). How does your circuit satisfy these parameters?
d. You implemented an integral controller because it is simple and stable. What other controllers could you have used? For one other type of controller how would it have been superior to your integral controller.
e. It the motor is spinning at a constant rate, give a definition of electrical power in terms of parameters of this lab? Research the term “mechanical power”. Give a definition of mechanical power. Are the electrical power and mechanical power related?

## Checkout (show this to the TA)

You should be able to demonstrate correct operation of the DC motor system. Be prepared to describe how your motor interface works. Demonstrate debugging features that allow you to visualize the software behavior. Show the TA the four modes specified in the Deliverables Section-4: Normal operation, Slow loop response time, Fast loop response time and Unstable mode.

All software and report files must be uploaded as instructed by your TA.

## Hints

1. You should use a periodic interrupt to determine if the motor is stopped or spinning very slowly.
8. The USB +5V regulated supply is specified to 500 mA total current. We strongly suggest you do not mechanically load the motor. It runs 120 mA unloaded, but much larger if you load the motor. If your PC disconnects you, then you will need to power cycle your computer and restart the OS.

Jonathan W. Valvano & Mark McDermott

Lab 10G DC Motor Control Fall 2022 Page 10.

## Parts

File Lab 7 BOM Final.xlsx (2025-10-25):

Bill of Materials |  |  | 2025-01-07 | "not free" means you have to buy it |  | "free sample" means you have to order it
ECE445L Spring 2025 |  |  | EE445L pays for the PCB | "Cabinet means in one of the six black cabinets in professsor's office (bring a print out of your SCH")
 |  |  |  | "Professor" means ask your professor quantity and style will vary (bring a print out of your SCH circuit)
Qty Note | REF DES Note (http://projects.ece.utexas.edu/valvano/wiki/doku.php?id=pcbartist:schematics) |  |  | "Box means in box in your professor's office (bring a print out of your SCH circuit)
Quantity | REF DES | Type | Description | Manufacturer | Mfg. P/N | Distributor | P/N | Unit cost | Cost | Where to get it? | Inventory
0 |  | ASM | 8-ohm speaker |  |  |  |  | $0.60 | $0.00 | professor
0 |  | ASM | 9V battery snap, T-type |  |  |  |  | $0.50 | $0.00 | Box
0 |  | ASM | Black case, 7.5" by 4.3" by 2.2" | Hammond | 1591ESBK | Mouser | 546-1591ES-BK | $5.18 | $0.00 | Box | http://www.hammondmfg.com/pdf/1591E.pdf
0 |  | ASM | Electret microphone | Panasonic |  |  |  | $0.50 | $0.00 | Cabinet
2 | C3,C9 | CAP | Ceramic, X7R, 20%, 1 uF |  |  | Jameco | 81509 | $0.35 | $0.70 | Cabinet
0 |  | CAP | Ceramic, Z5U, -20/+80%, 0.47 uF | Kemet | C320C474M5U5TA | Digikey | 399-4309-ND | $0.40 | $0.00 | Cabinet
4 | C4,C6,C7,C8 | CAP | Ceramic, Z5U, -20/+80%, 0.1 uF |  |  | Digikey | 399-4151-ND | $0.04 | $0.18 | Cabinet
0 |  | CAP | Ceramic, Z5U, -20/+80%, 0.033 uF |  |  | Digikey | 399-4298-ND | $0.40 | $0.00 | Cabinet
0 |  | CAP | Ceramic, Z5U, -20/+80%, 0.027uF |  |  |  |  | $0.40 | $0.00 | Cabinet
2 | C11,C5 | CAP | Ceramic, Z5U, -20/+80%, 0.01 uF |  |  | Digikey | 399-4148-ND | $0.40 | $0.80 | Cabinet
0 |  | CAP | Ceramic, Z5U, -20/+80%, 4.7 nF |  |  | Digikey | 399-4188-ND | $0.40 | $0.00 | Cabinet
0 |  | CAP | Ceramic, Z5U, -20/+80%, 2.2 nF |  |  |  |  | $0.40 | $0.00 | Cabinet
0 |  | CAP | Ceramic, Z5U, -20/+80%, 1 nF |  |  |  |  | $0.40 | $0.00 | Cabinet
0 |  | CAP | Ceramic Z5U, -20/+80%, 470 pF |  |  |  |  | $0.03 | $0.00 | Cabinet
0 |  | CAP | Ceramic Z5U, -20/+80%, 330 pF |  |  |  |  | $0.03 | $0.00 | Cabinet
0 |  | CAP | Ceramic Z5U, -20/+80%, 220 pF |  |  |  |  | $0.03 | $0.00 | Cabinet
0 |  | CAP | Ceramic Z5U, -20/+80%, 100 pF |  |  |  |  | $0.03 | $0.00 | Cabinet
0 |  | CAP | Ceramic Z5U, -20/+80%, 22 pF |  |  | Jameco | 15405 | $0.03 | $0.00 | Cabinet
2 | C1,C2 | CAP | Ceramic C0G, 10%, 10 pF | Murata 50V 5% | RDE5C1H100J0P1H03B | Digikey | 490-8629-ND | $0.31 | $0.62 | Cabinet | not required, we expect most students will create a system with the LaunchPad
1 | C10 | CAP-Tant | Tantalum, 16V, 20% 2.2 uF | AVX Corporation | TAP225M016CCS | Digikey | 478-8819-ND | $0.29 | $0.29 | Cabinet
5 | C12,C13,C14,C15 | CAP-Tant | Tantalum, 16V, 10% 4.7 uF |  |  | Digikey | 478-1904-ND | $0.22 | $1.10 | Cabinet
0 |  | CAP-Tant | Tantalum, 20V, 10%, 1 uF |  |  | Digikey | 478-1833-ND | $0.32 | $0.00 | Cabinet
0 |  | CAP-Tant | Tantalum, 10UF 20V 10% |  |  | Digikey | 478-1840-ND | $0.56 | $0.00 | Cabinet
0 |  | CAP-Tant | Tantalum, 35V, 10%, 0.47 uF |  |  | Jameco | 33531 | $0.19 | $0.00 | Cabinet
0 |  | CAP-Elec | Electrolytic, 16V, 100 uF, cap 20%, ESR=20mV |  |  | Mouser | 661-APSF160E101MF05S | $0.38 | $0.00 | Cabinet
0 |  | CON | 2 to 40 pin 0.1 in header (price per pin) |  |  | AllElectronics | SHS-40 | $0.02 | $0.00 | Cabinet
1 |  | CON | 2-pin header |  |  | AllElectronics | SBH-2 | $0.10 | $0.10 | Cabinet
0 |  | CON | 2-pin jumper |  |  | AllElectronics | SBC-2 | $0.27 | $0.00 | Cabinet
1 | J2 | CON | 2-pin jumper |  |  | AllElectronics | SJ-1 | $0.10 | $0.10 | Cabinet
1 | TP2 | CON | Test point, black | Keystone Electronics | 5001 | Digikey | 36-5001K-ND | $0.23 | $0.23 | Cabinet
0 |  | CON | Test point, orange | Keystone Electronics | 5003 | Digikey | 36-5003K-ND | $0.23 | $0.00 | Cabinet
0 |  | CON | Test point, yellow | Keystone Electronics | 5004 | Digikey | 36-5004K-ND | $0.23 | $0.00 | Cabinet
1 | TP4 | CON | Test point, white | Keystone Electronics | 5002 | Digikey | 36-5002K-ND | $0.23 | $0.23 | Cabinet
0 |  | CON | Test point, blue | Keystone Electronics | 5117 | Digikey | 36-5117-ND | $0.23 | $0.00 | Cabinet
0 |  | CON | Test point, green | Keystone Electronics | 5116 | Digikey | 36-5116-ND | $0.23 | $0.00 | Cabinet
2 | TP1,TP3 | CON | Test point, red | Keystone Electronics | 5000 | Digikey | 36-5000K-ND | $0.23 | $0.46 | Cabinet
1 |  | CON | 10-pin LCD connector | SamTec | BCS-110-L-S-TE | SamTec |  |  | $0.00 | Cabinet
0 |  | CON | 14-pin LCD connector | SamTec | BCS-114-L-S-TE | SamTec |  |  | $0.00 | Cabinet
0 |  | CON | 16-pin LCD connector | SamTec | BCS-116-L-S-TE | SamTec |  |  | $0.00 | Cabinet
0 |  | CON | 20-pin LCD connector | SamTec | BCS-120-L-S-TE | SamTec |  |  | $0.00 | Cabinet
0 |  | CON | Socket for micro SD card | Molex | 473340001 | Digikey | WM3288CT-ND | $4.02 | $0.00 | professor | do not use, rather included on ST7735
1 |  | CON | USB Mini-B socket, board mount, surface mount | Molex | 56579-0576 | Mouser | 538-56579-0576 | $2.46 | $2.46 | Cabinet
0 |  | CON | Micro USB Type B, surface mount | Hirose Connector | ZX62D-B-5PA8(30) | Mouser | 798-ZX62D-B-5PA830 | $0.47 | $0.00 | Cabinet
0 |  | CON | USB Mini-B socket, board mount, through hole | Molex | 54819-0519 | Digikey | WM17115-ND | $0.65 | $0.00 | Cabinet
0 |  | CON | BoosterPack connector | FCI | 68021-208HLF | Digikey | 609-3243-ND | $0.26 | $0.00 | Cabinet
1 | J4 | CON | Logic Analyzer connector | FCI | 68021-208HLF | Digikey | 609-3344-ND | $0.27 | $0.27 | Cabinet
1 | J1 | CON | JTAG 1 by 5 male header |  |  |  |  | $0.29 | $0.29 | Cabinet
0 |  | CON | 10 pin 2mm socket for Xbee (need two) | SamTec | SQT-110-01-F-S | SamTec |  | $1.00 | $0.00 | Cabinet
0 |  | CON | DB9 serial connector, female, board mount |  |  | Jameco | 15771 | $0.65 | $0.00 | Cabinet
2 | U1 | CPU | TM4C123GH6PM 64-pin LQFP | TI | TM4C123GH6PMI | Mouser | 595-TM4C123GH6PMI | $11.55 | $23.10 | not required, we expect most students will create a system with the LaunchPad
1 | Y1 | CRYS | NX5032GA-16.000000 | NDK | NX5032GA-16.000000 | Digikey | 644-1037-1-ND | $0.51 | $0.51 | Cabinet | not required, we expect most students will create a system with the LaunchPad
3 | D4 | DIODE | 1N914 diode | Fairchild | 1N914 | Digikey | 1N914B-ND | $0.05 | $0.15 | Cabinet
0 |  | IC | ACCELER DUAL-AX 2.0G 8PLCC | Analog Devices | ADXL202JQC | Quest Components | ADXL202JQC | $7.50 | $0.00 | professor
1 | U3 | IC | LM2937 3.3 V regulator TO220, 500mA | TI | LM2937ET-3.3/NOPB | Digikey | LM2937ET-3.3-ND | $1.17 | $1.17 | Cabinet
0 |  | IC | LP2950 3.3V regulator, 100 mA TO-92 | TI | LP2950-33LPRE3 | Digikey | 296-31455-1-ND | $0.19 | $0.19 | Cabinet
1 | U6 | IC | 78M05 500mA 5V TO-220 regulator | National | LM78M05 | Jameco | 192233 | $0.19 | $0.19 | Cabinet
0 |  | IC | OPA4350 quad op amp | TI | OPA4350 | TI |  |  | $0.00 | free sample
0 |  | IC | TLV5616 12-bit DAC | TI | TLV5616 | TI | TLV5616CP |  | $0.00 | Cabinet or free sample
0 |  | IC | TLV5618 dual 12-bit DAC | TI | TLV5618 | TI | TLV5618ACP |  | $0.00 | free sample
0 |  | IC | MAX539 12-bit DAC | Maxim-IC | MAX539 | Maxim | MAX539ACPA |  | $0.00 | free sample
0 |  | IC | MAX1247 12-bit ADC | Maxim-IC | MAX1247 | Maxim | MAX1247ACPE+ |  | $0.00 | free sample
0 |  | IC | INA122P instrumentation amp | TI | INA122P | TI | INA122P |  | $0.00 | Cabinet or free sample
0 |  | IC | OPA2350 dual op amp | TI | OPA2350PA | TI | OPA2350PA |  | $0.00 | Cabinet or free sample |  |  | 1 KD
0 |  | IC | TLC2274 quad op amp | TI | TLC2274ACN | TI | TLC2274ACN | $1.17 | $0.00 | free sample |  |  | 2 HD
0 |  | IC | TPA731 audio amp (pin 1 low) 700mW | TI | TPA731D | TI | TPA731D | $1.84 | $0.00 | Cabinet or free sample |  |  | 3 AD
0 |  | IC | TPA751 audio amp (pin 1 high) 700mW | TI | TPA751D | TI | TPA751D | $1.84 | $0.00 | free sample |  |  | 4 JD
0 |  | IC | LM4041CILPR shunt diode reference | TI | LM4041CILPR | TI | LM4041CILPR | $0.90 | $0.00 | Cabinet or free sample |  |  | 5 CD
0 |  | IC | AD8032 dual op amp | Analog Devices | AD8032ANZ | Analog Devices | AD8032ANZ | $4.47 | $0.00 | free sample |  |  | 6 BD
0 |  | IC | L293 Motor H bridge | TI | L293NE | Digikey | 296-9519-5-ND | $3.50 | $0.00 | not free |  |  | 7 MD
0 |  | IC | DRV8848 | TI | DRV8848PWP | TI
0 |  | IC | 74HC595 |  |  | Jameco | 46105 | $0.40 | $0.00 | Cabinet |  |  | 8 ED
0 |  | IC | 74HC165 |  |  | Jameco | 45495 | $0.30 | $0.00 | Cabinet |  |  | 9 FD
0 |  | IC | 74HCT125N | TI | SN74HCT125N | Mouser | 595-SN74HCT125N | $0.53 | $0.00 | Cabinet |  |  | 9 FD
0 |  | IC | RS232 driver | STMicroelectronics | ST232CN | Jameco | 2001171 | $0.58 | $0.00 | not free |  |  | 0 ND
0 |  | JACK | DC Power MALE 2.1mm |  |  | Jameco | 101179 | $0.55 | $0.00 | Cabinet |  |  | * LD
0 |  | JACK | Stereo Jack, or audio jack |  |  | AllElectronics | MJW-12 | $0.09 | $0.00 | Cabinet |  | 87YY3212A
0 |  | KEY | 3 by 4 common bus (D), keypad | Grayhill | 87YY3212A-506 | BGMicro | SWT1109 | $2.99 | $0.00 | Box | http://docs.bgmicro.com/pdf/swt1109.pdf
0 |  | LCD | 84 by 48 LCD | Nokia | 5110 | Sparkfun | 10168 | $9.95 | $0.00 | not free
1 | U2 | LCD | 18-bit color 128*160 1.8" TFT LCD display | Sitronix | ST7735R | Adafruit | 358 | $19.96 | $19.96 | not free
1 | D3 | LED | Green 2mA 5mm diffused | Avago Technologies | HLMP-4740 | Digikey | 516-1327-ND | $0.29 | $0.29 | Cabinet
1 | D2 | LED | Red 1.6V 1mA 5mm diffused | Avago Technologies | HLMP-D150 | Digikey | 516-1323-ND | $0.29 | $0.29 | Cabinet
0 |  | LED | Yellow 2mA 5mm diffused | Avago Technologies | HLMP-4719 | Digikey | 516-1326-ND | $0.29 | $0.00 | Cabinet
0 |  | LED | Orange 10mA 5mm diffused | Avago Technologies | HLMP-D401 | Digikey | 516-1330-ND | $0.29 | $0.00 | Cabinet
0 |  | LED | Blue 10mA 5mm diffused |  |  |  |  | $0.99 | $0.00 | Cabinet | warning, the blue LEDs are very bright
0 |  | PCB | PCB plus shipping | JLCPCB |  | JLCPCB |  | $20.00 | $0.00 |  | http://www.4pcb.com/
0 |  | POT | 20K LINEAR SLIDE POT |  |  |  |  | $0.33 | $0.00 | professor
2 |  | POT | 10 K one-turn potentiometer |  |  |  |  | $0.15 | $0.30 | Cabinet
0 |  | POT | 20 K one-turn potentiometer |  |  |  |  | $0.15 | $0.00 | Cabinet
0 |  | RES | Carbon 1/6W, 5%, 100 | Yageo | CFR-12JB-100R | Digikey | 100EBK-ND | $0.02 | $0.00 | Cabinet
0 |  | RES | Carbon 1/6W, 5%, 220 | Yageo | CFR-12JB-220R | Digikey | 220EBK-ND | $0.02 | $0.00 | Cabinet
0 |  | RES | Carbon 1/6W, 5%, 270 | Yageo | CFR-12JB-270R | Digikey | 270EBK-ND | $0.02 | $0.00 | Cabinet
1 | R5 | RES | Carbon 1/6W, 5%, 330 | Yageo | CFR-12JB-330R | Digikey | 330EBK-ND | $0.02 | $0.02 | Cabinet
0 |  | RES | Carbon 1/6W, 5%, 470 | Yageo | CFR-12JB-470R | Digikey | 470EBK-ND | $0.02 | $0.00 | Cabinet
0 |  | RES | Carbon 1/6W, 5%, 510 | Yageo | CFR-12JB-510R | Digikey | 510EBK-ND | $0.02 | $0.00 | Cabinet
0 |  | RES | Carbon 1/6W, 5%, 680 | Yageo | CFR-12JB-680R | Digikey | 680EBK-ND | $0.02 | $0.00 | Cabinet
1 | R6 | RES | Carbon 1/6W, 5%, 820 | Yageo | CFR-12JB-820R | Digikey | 820EBK-ND | $0.02 | $0.02 | Cabinet
0 |  | RES | Carbon 1/6W, 5%, 1K | Yageo | CFR-12JB-1K0 | Digikey | 1.0KEBK-ND | $0.02 | $0.00 | Cabinet
0 |  | RES | Carbon 1/6W, 5%, 1.2K | Yageo | CFR-12JB-1K2 | Digikey | 1.2KEBK-ND | $0.02 | $0.00 | Cabinet
0 |  | RES | Carbon 1/6W, 5%, 1.5K | Yageo | CFR-12JB-1K5 | Digikey | 1.5KEBK-ND | $0.02 | $0.00 | Cabinet
0 |  | RES | Carbon 1/6W, 5%, 1.8K | Yageo | CFR-12JB-1K8 | Digikey | 1.8KEBK-ND | $0.02 | $0.00 | Cabinet
0 |  | RES | Carbon 1/6W, 5%, 2.0K | Yageo | CFR-12JB-2K0 | Digikey | 2.0KEBK-ND | $0.02 | $0.00 | Cabinet
0 |  | RES | Carbon 1/6W, 5%, 2.2K | Yageo | CFR-12JB-2K2 | Digikey | 2.2KEBK-ND | $0.02 | $0.00 | Cabinet
0 |  | RES | Carbon 1/6W, 5%, 2.7K | Yageo | CFR-12JB-2K7 | Digikey | 2.7KEBK-ND | $0.02 | $0.00 | Cabinet
0 |  | RES | Carbon 1/6W, 5%, 3.3K | Yageo | CFR-12JB-3K3 | Digikey | 3.3KEBK-ND | $0.02 | $0.00 | Cabinet
0 |  | RES | Carbon 1/6W, 5%, 3.9K | Yageo | CFR-12JB-3K9 | Digikey | 3.9KEBK-ND | $0.02 | $0.00 | Cabinet
0 |  | RES | Carbon 1/6W, 5%, 4.7K | Yageo | CFR-12JB-4K7 | Digikey | 4.7KEBK-ND | $0.02 | $0.00 | Cabinet
0 |  | RES | Carbon 1/6W, 5%, 5.1K | Yageo | CFR-12JB-5K1 | Digikey | 5.1KEBK-ND | $0.02 | $0.00 | Cabinet
0 |  | RES | Carbon 1/6W, 5%, 5.6K | Yageo | CFR-12JB-5K6 | Digikey | 5.6KEBK-ND | $0.02 | $0.00 | Cabinet
0 |  | RES | Carbon 1/6W, 5%, 6.8K | Yageo | CFR-12JB-6K8 | Digikey | 6.8KEBK-ND | $0.02 | $0.00 | Cabinet
0 |  | RES | Carbon 1/6W, 5%, 8.2K | Yageo | CFR-12JB-8K2 | Digikey | 8.2KEBK-ND | $0.02 | $0.00 | Cabinet
3 | R2,R3,R7 | RES | Carbon 1/6W, 5%, 10K | Yageo | CFR-12JB-10K | Digikey | 10KEBK-ND | $0.02 | $0.07 | Cabinet
0 |  | RES | Carbon 1/6W, 5%, 12K | Yageo | CFR-12JB-12K | Digikey | 12KEBK-ND | $0.02 | $0.00 | Cabinet
0 |  | RES | Carbon 1/6W, 5%, 15K | Yageo | CFR-12JB-15K | Digikey | 15KEBK-ND | $0.02 | $0.00 | Cabinet | http://www.kemet.com/kemet/web/homepage/kechome.nsf/vapubfiles/F3101_GoldMax.pdf/$file/F3101_GoldMax.pdf
0 |  | RES | Carbon 1/6W, 5%, 18K | Yageo | CFR-12JB-18K | Digikey | 18KEBK-ND | $0.02 | $0.00 | Cabinet
0 |  | RES | Carbon 1/6W, 5%, 20K | Yageo | CFR-12JB-20K | Digikey | 20KEBK-ND | $0.02 | $0.00 | Cabinet
0 |  | RES | Carbon 1/6W, 5%, 22K | Yageo | CFR-12JB-22K | Digikey | 22KEBK-ND | $0.02 | $0.00 | Cabinet
0 |  | RES | Carbon 1/6W, 5%, 27K | Yageo | CFR-12JB-27K | Digikey | 27KEBK-ND | $0.02 | $0.00 | Cabinet
0 |  | RES | Carbon 1/6W, 5%, 36K | Yageo | CFR-12JB-36K | Digikey | 36KEBK-ND | $0.02 | $0.00 | Cabinet
0 |  | RES | Carbon 1/6W, 5%, 33K | Yageo | CFR-12JB-33K | Digikey | 33KEBK-ND | $0.02 | $0.00 | Cabinet
0 |  | RES | Carbon 1/6W, 5%, 39K | Yageo | CFR-12JB-39K | Digikey | 39KEBK-ND | $0.02 | $0.00 | Cabinet
0 |  | RES | Carbon 1/6W, 5%, 47K | Yageo | CFR-12JB-47K | Digikey | 47KEBK-ND | $0.02 | $0.00 | Cabinet
0 |  | RES | Carbon 1/6W, 5%, 51K | Yageo | CFR-12JB-51K | Digikey | 51KEBK-ND | $0.02 | $0.00 | Cabinet
0 |  | RES | Carbon 1/6W, 5%, 56K | Yageo | CFR-12JB-56K | Digikey | 56KEBK-ND | $0.02 | $0.00 | Cabinet
0 |  | RES | Carbon 1/6W, 5%, 68K | Yageo | CFR-12JB-68K | Digikey | 68KEBK-ND | $0.02 | $0.00 | Cabinet
0 |  | RES | Carbon 1/6W, 5%, 82K | Yageo | CFR-12JB-82K | Digikey | 82KEBK-ND | $0.02 | $0.00 | Cabinet
0 |  | RES | Carbon 1/6W, 5%, 100K | Yageo | CFR-12JB-100K | Digikey | 100KEBK-ND | $0.02 | $0.00 | Cabinet
0 |  | RES | Carbon 1/6W, 5%, 120K | Yageo | CFR-12JB-120K | Digikey | 120KEBK-ND | $0.02 | $0.00 | Cabinet
0 |  | RES | Carbon 1/6W, 5%, 150K | Yageo | CFR-12JB-150K | Digikey | 150KEBK-ND | $0.02 | $0.00 | Cabinet
0 |  | RES | Carbon 1/6W, 5%, 180K | Yageo | CFR-12JB-180K | Digikey | 180KEBK-ND | $0.02 | $0.00 | Cabinet
0 |  | RES | Carbon 1/6W, 5%, 200K | Yageo | CFR-12JB-200K | Digikey | 200KEBK-ND | $0.02 | $0.00 | Cabinet
0 |  | RES | Carbon 1/6W, 5%, 220K | Yageo | CFR-12JB-220K | Digikey | 220KEBK-ND | $0.02 | $0.00 | Cabinet
0 |  | RES | Carbon 1/6W, 5%, 240K | Yageo | CFR-12JB-240K | Digikey | 240KEBK-ND | $0.02 | $0.00 | Cabinet
0 |  | RES | Carbon 1/6W, 5%, 270K | Yageo | CFR-12JB-270K | Digikey | 270KEBK-ND | $0.02 | $0.00 | Cabinet
0 |  | RES | Carbon 1/6W, 5%, 330K | Yageo | CFR-12JB-330K | Digikey | 330KEBK-ND | $0.02 | $0.00 | Cabinet
0 |  | RES | Carbon 1/6W, 5%, 390K | Yageo | CFR-12JB-390K | Digikey | 390KEBK-ND | $0.02 | $0.00 | Cabinet
0 |  | RES | Carbon 1/6W, 5%, 470K | Yageo | CFR-12JB-470K | Digikey | 470KEBK-ND | $0.02 | $0.00 | Cabinet
0 |  | RES | Carbon 1/6W, 5%, 510K | Yageo | CFR-12JB-510K | Digikey | 510KEBK-ND | $0.02 | $0.00 | Cabinet
0 |  | RES | Carbon 1/6W, 5%, 560K | Yageo | CFR-12JB-560K | Digikey | 560KEBK-ND | $0.02 | $0.00 | Cabinet
0 |  | RES | Carbon 1/6W, 5%, 680K | Yageo | CFR-12JB-680K | Digikey | 680KEBK-ND | $0.02 | $0.00 | Cabinet
0 |  | RES | Carbon 1/6W, 5%, 820K | Yageo | CFR-12JB-820K | Digikey | 820KEBK-ND | $0.02 | $0.00 | Cabinet
1 | R1 | RES | Carbon 1/6W, 5%, 1M | Yageo | CFR-12JB-1M0 | Digikey | 1.0MEBK-ND | $0.02 | $0.02 | Cabinet
0 |  | RES | Carbon 1/6W, 5%, 10M | Yageo | CFR-12JB-10M | Digikey | 10MEBK-ND | $0.02 | $0.00 | Cabinet
2 | SW1, SW2 | SW | Tactile Switch, surface mount | C&K Components | KSC353JLFG | Mouser | 611-KSC353JLFG | $0.86 | $1.72 | Cabinet
0 |  | SW | B3F tactile push button switch | Omron Electronics | B3F-1052 | Digikey | SW405-ND | $0.17 | $0.00 | Cabinet
0 |  | SW | Black Off board momentary push buttom |  |  |  |  | $0.35 | $0.00 | Cabinet
0 |  | SW | Red Off board momentary push buttom |  |  |  |  | $0.35 | $0.00 | Cabinet
0 |  | SW | On/off power switch |  |  | BGMicro | SWT1010 | $0.85 | $0.00 | Cabinet
0 |  | TRAN | PN2222 NPN transistor | Fairchild Semiconductor | PN2222 | Digikey | PN2222BU-ND | $0.13 | $0.00 | Cabinet | be careful to get pins 1 and 3 correct, there are two versions of the chip: 2N2222 and PN2222
0 |  | TRAN | TIP120 Darlington NPN, TO220 | Fairchild | TIP120 | Digikey | TIP120-ND | $0.68 | $0.00 | Cabinet
0 |  | TRAN | TIP125 Darlington PNP, TO220 | Fairchild | TIP125 | Digikey | TIP125TU-ND | $0.67 | $0.00 | Cabinet
0 |  | TRAN | IRF540 MOSFET N-channel, TO220 |  | IRF540 | Digikey | IRF540NPBF-ND | $1.95 | $0.00 | professor
2 | Q1, Q2 | TRAN | IRLD120PBF | N-MOSFET | DIP-4 | Mouser | 844-IRLD120PBF | $1.58 | $3.16
3 | U4, U5,U7 | IC | Ultrasonic Distance Sensor | HiLetGo | HC-SR04 | Amazon | HC-SR04 | $1.83 | $5.49 | not free | https://www.amazon.com/HiLetgo-HC-SR04-Ultrasonic-Distance-MEGA2560/dp/B00E87VXH0
2 |  | TOY | Rhode Island Novelty 1.5 Inch Plastic Ping Pong Ball, Pack of 12 | Rhode Island Novelty |  | Amazon |  | $5.09 | $0.00 | free | https://www.amazon.com/Rhode-Island-Novelty-Plastic-PING/dp/B003EDWJNQ?rnid=2470954011&rps=1
2 |  | TOY | MECCANIXITY Acrylic Pipe Clear Rigid Round Tube 42mm(1.6") ID 45mm(1 3/4") OD 6" for Lamps and Lanterns, Water Cooling System | MECCANIXITY |  | Amazon |  | $12.19 | $24.38 | not free | https://www.amazon.com/MECCANIXITY-Acrylic-Lanterns-Cooling-System/dp/B0B9BZ8Z6S
2 | J2, J6 | MOTOR | Brushed Motors | EUDAX |  | Amazon | B08GPPJR1T | $2.04 | $4.08 | not free | https://www.amazon.com/dp/B08GPPJR1T?ref=ppx_yo2ov_dt_b_fed_asin_title
0 |  | IC | TF Luna LIDAR sensor (too expensive) | Mouser | SJ-GU-TF-Luna A01 | Mouser | A01 | $25.98 | $0.00 | not free | https://www.amazon.com/Benewake-TF-Luna-Single-Point-Ranging-Interface/dp/B086MJQSLR
0 |  | CON | 4 pin connectors | Wowoone |  | Amazon |  | $8.49 | $8.49 | not free | https://www.amazon.com/WOWOONE-Connector-Female-Cables-Batteries/dp/B08R9VVD6L?cv_ct_cx=4+pin+female+connector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
2 | J8,J9 | IC | Adafruit USBC Breakout | Adafruit |  | Adafruit |  | $2.50 | $2.50 | not free | https://www.adafruit.com/product/4090
 |  |  |  |  |  |  |  |  | $103.94
 |  |  |  |  |  |  |  |  | $60.88
 |  |  |  |  |  |  |  |  | $44.94

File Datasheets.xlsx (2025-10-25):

Part Name | Part/SKU No. | Datasheet link | CAD Files | Other documents (important)
Ultrasonic Sensor | HC-SR04 | https://cdn.sparkfun.com/datasheets/Sensors/Proximity/HCSR04.pdf | https://www.handsontec.com/dataspecs/HC-SR04-Ultrasonic.pdf | https://www.handsontec.com/dataspecs/HC-SR04-Ultrasonic.pdf
Motor (maybe?) | 775 |  |  | https://www.handsontec.com/dataspecs/motor_fan/775-Motor.pdf

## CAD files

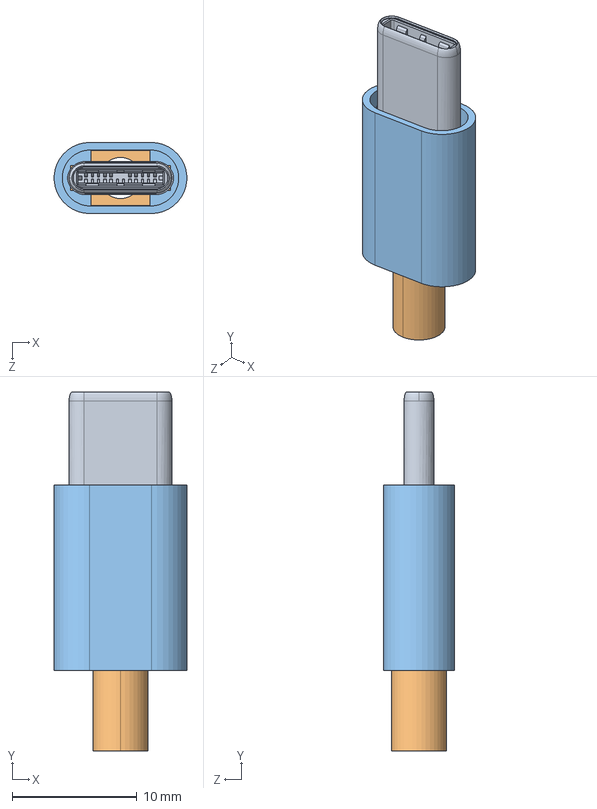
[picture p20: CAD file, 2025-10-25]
hw/assembly cad/USB-c/USB C Male Assembly.SLDASM
10.6 x 28.8 x 5.70 mm
USB C Male Cover
USB C Male Wire Tube
USB C Male Connector Board

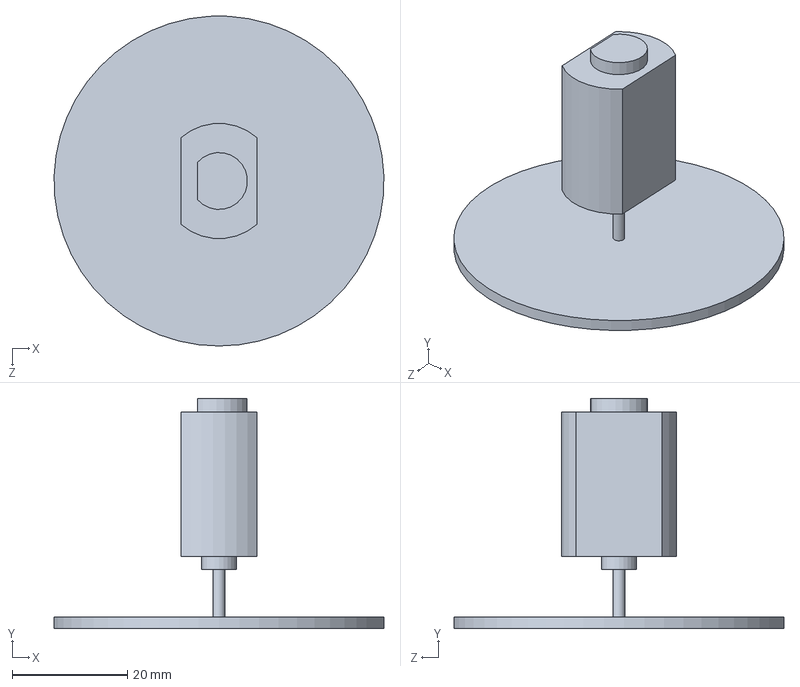
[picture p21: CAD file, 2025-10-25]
hw/assembly cad/motor.SLDPRT
57.2 x 40.0 x 57.2 mm

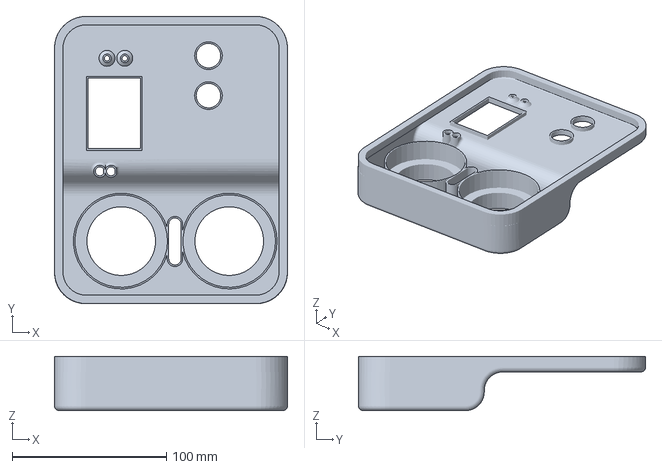
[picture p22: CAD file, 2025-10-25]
hw/assembly cad/STL files/lid2.3mf
151.0 x 186.1 x 35.0 mm

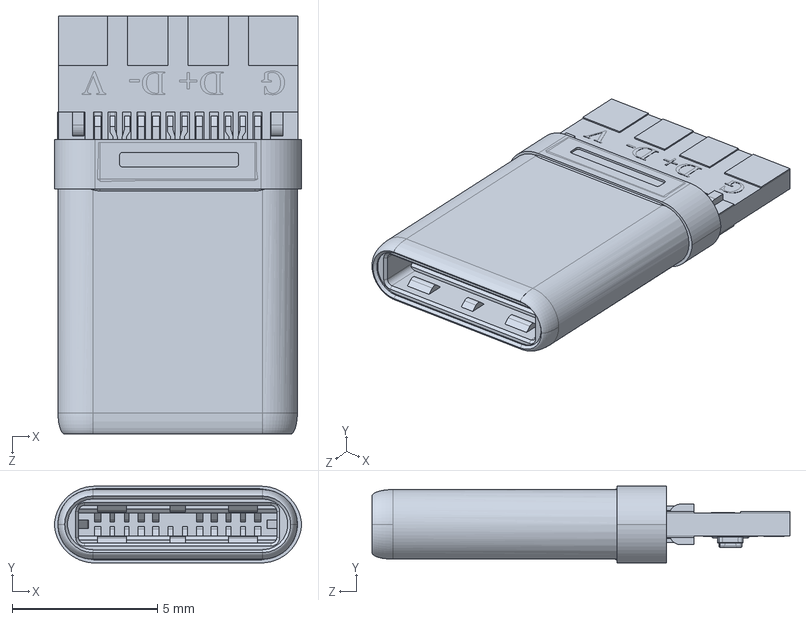
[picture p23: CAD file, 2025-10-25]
hw/assembly cad/USB-c/USB C Male Connector Board.SLDPRT
8.52 x 2.65 x 14.4 mm

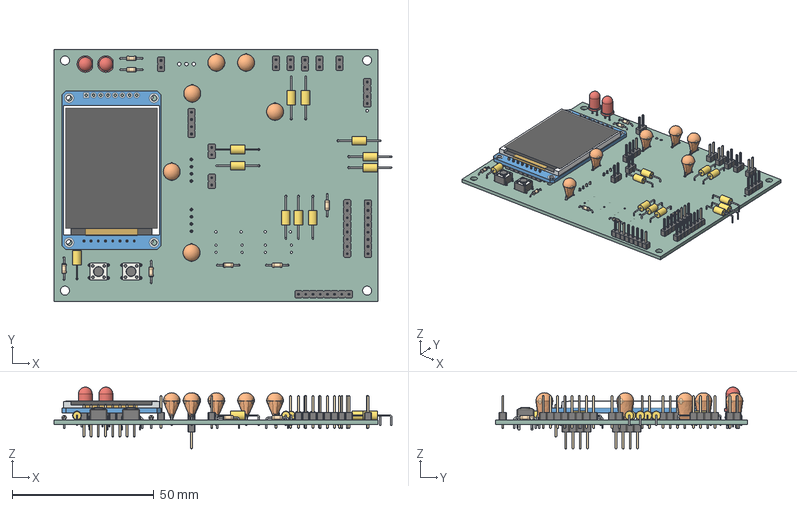
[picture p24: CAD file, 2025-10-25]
hw/ECE445L_Lab7/model.step
119.3 x 88.9 x 21.8 mm
CP_Radial_Tantal_D60mm_P500mm x 6
C_Axial_L51mm_D31mm_P1500mm_Horizontal x 11
PinHeader_1x02_P254mm_Vertical x 8
R_Axial_DIN0204_L36mm_D16mm_P762mm_Horizontal x 7
PinHeader_1x04_P254mm_Vertical x 4
SW_PUSH_6mm x 2
LED_D5.0mm x 2
PinHeader_1x08_P254mm_Vertical x 4
1.8_inches_128x160_RGB_TFT_LCD
ECE445L_Lab7_PCB

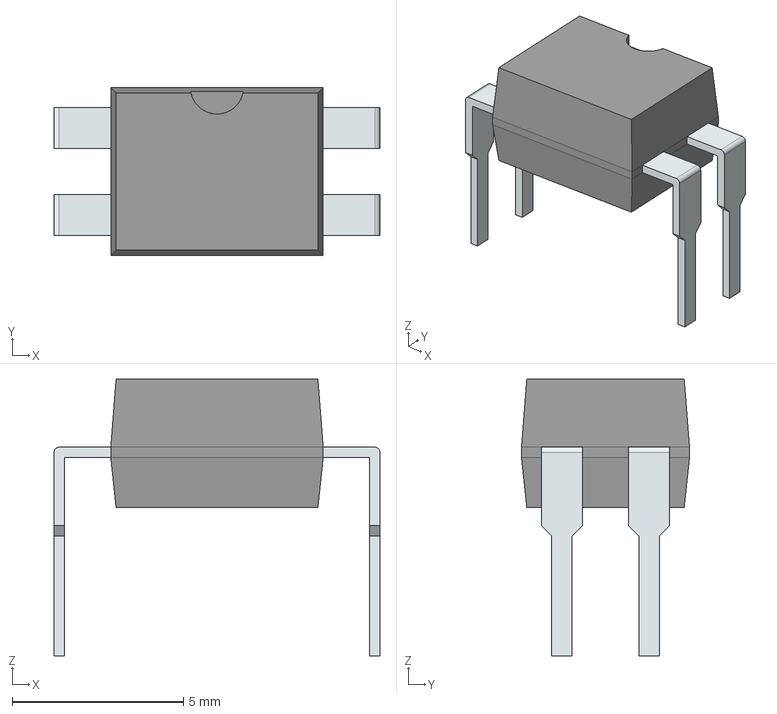
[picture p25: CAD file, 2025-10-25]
hw/ECE445L_Lab7/models/vishay_IRLD024PBF.stp
9.51 x 4.90 x 8.07 mm
PinsArrayLR

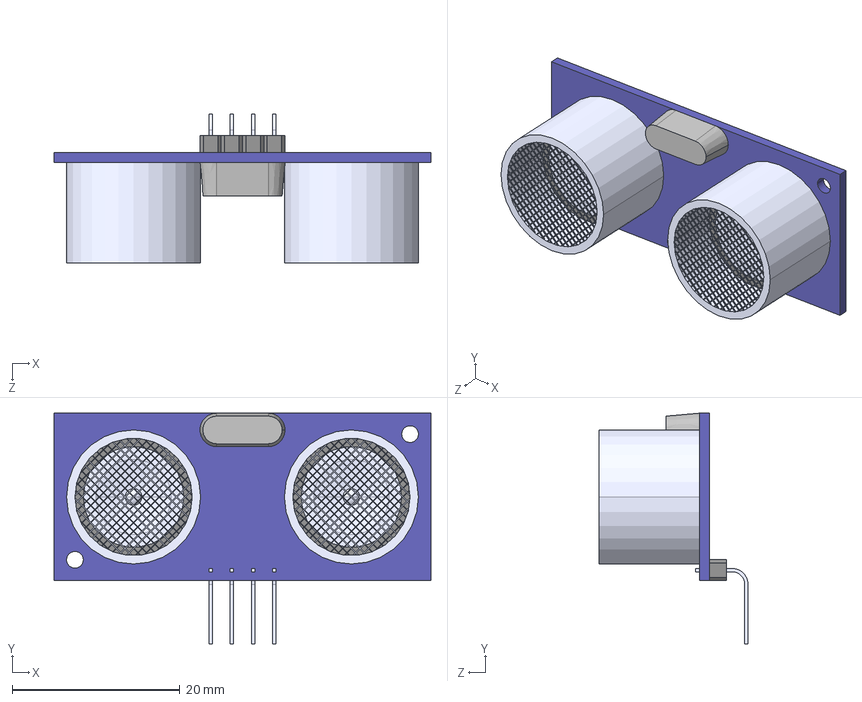
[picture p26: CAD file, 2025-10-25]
hw/Part Libraries/HC-SR04/HC-SR04.step
45.0 x 27.5 x 17.8 mm

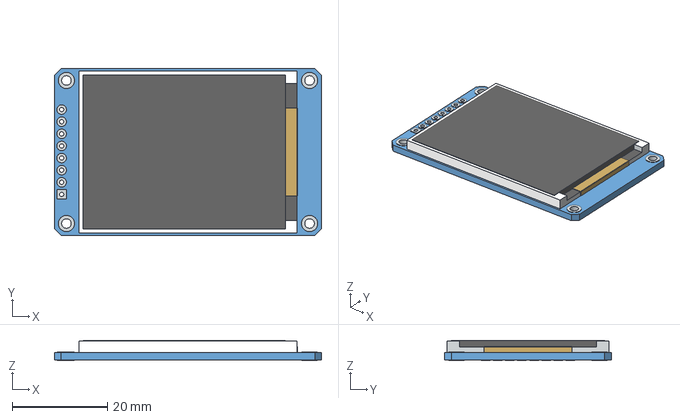
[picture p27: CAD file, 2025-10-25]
hw/Part Libraries/models/adafruit_st7735r.stp
56.0 x 35.0 x 4.25 mm

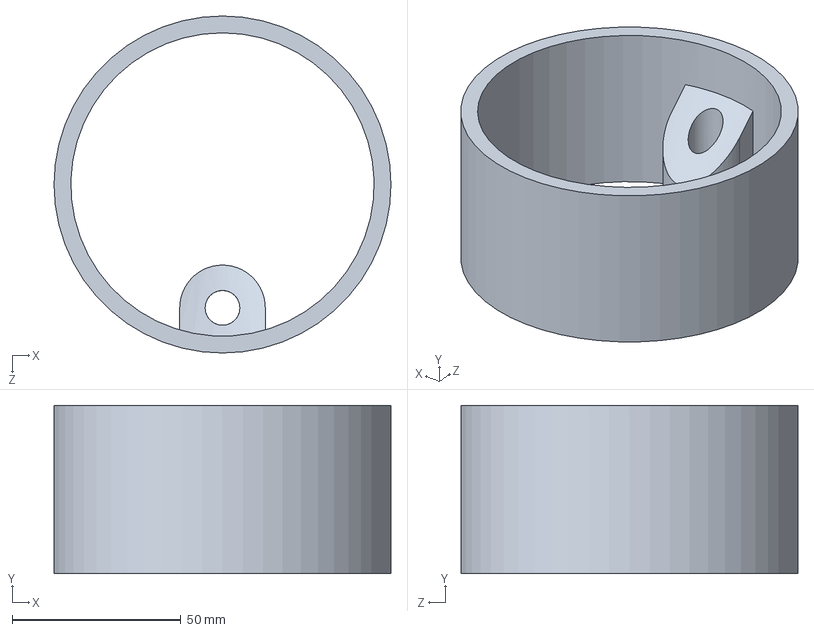
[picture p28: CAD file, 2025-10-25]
hw/assembly cad/motor mount.SLDPRT
100.0 x 50.0 x 100.0 mm

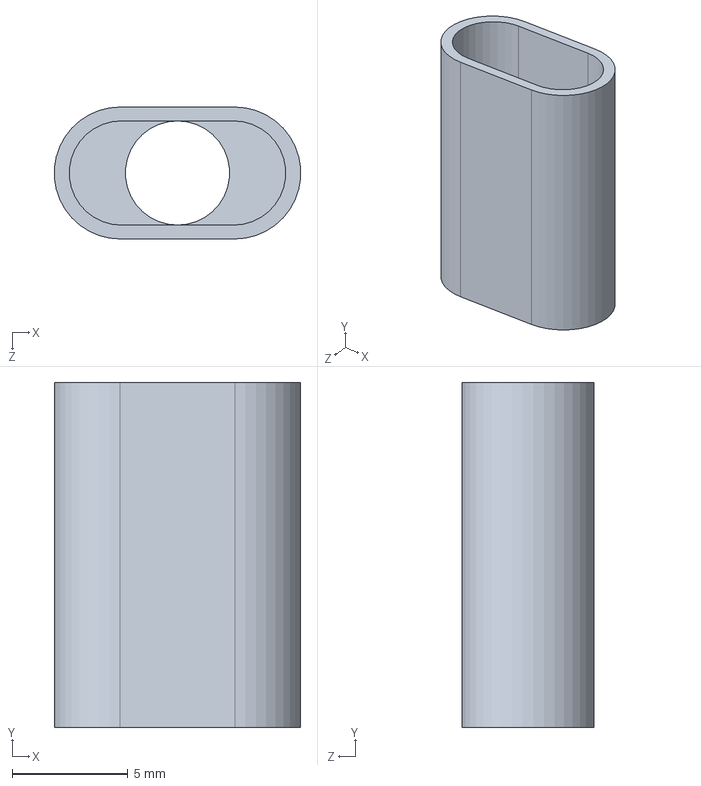
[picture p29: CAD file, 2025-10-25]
hw/assembly cad/USB-c/USB C Male Cover.SLDPRT
10.6 x 14.9 x 5.70 mm

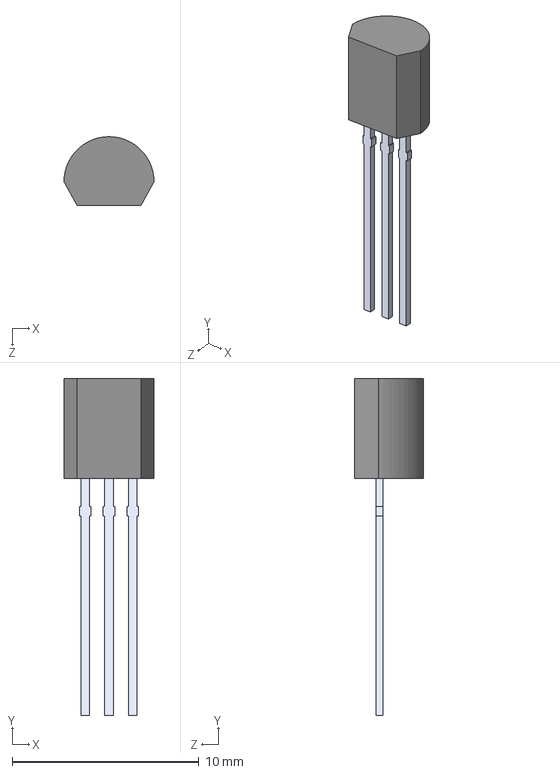
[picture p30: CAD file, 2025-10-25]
hw/ECE445L_Lab7/models/ti_LM4041CILPR.step
4.82 x 18.0 x 3.68 mm

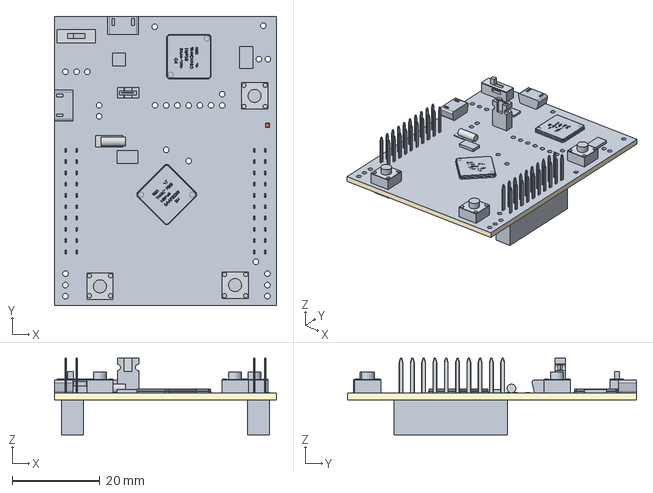
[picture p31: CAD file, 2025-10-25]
hw/Part Libraries/models/ti_EKTM4C123GXL.step
50.8 x 66.0 x 17.5 mm

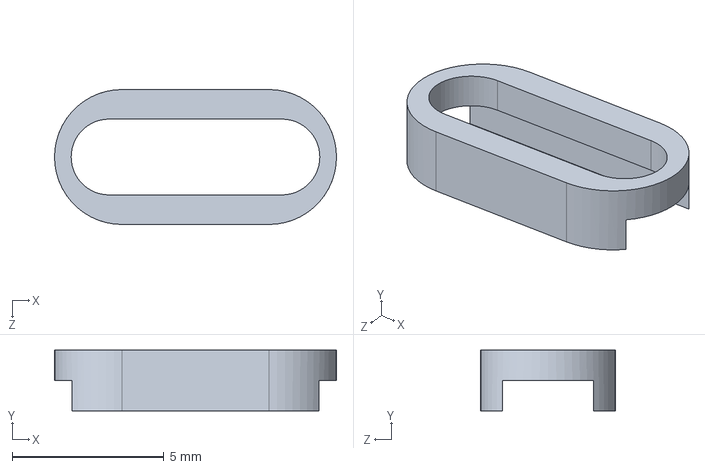
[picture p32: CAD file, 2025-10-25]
hw/assembly cad/USB C Male Top Cover.STEP
9.30 x 2.00 x 4.45 mm

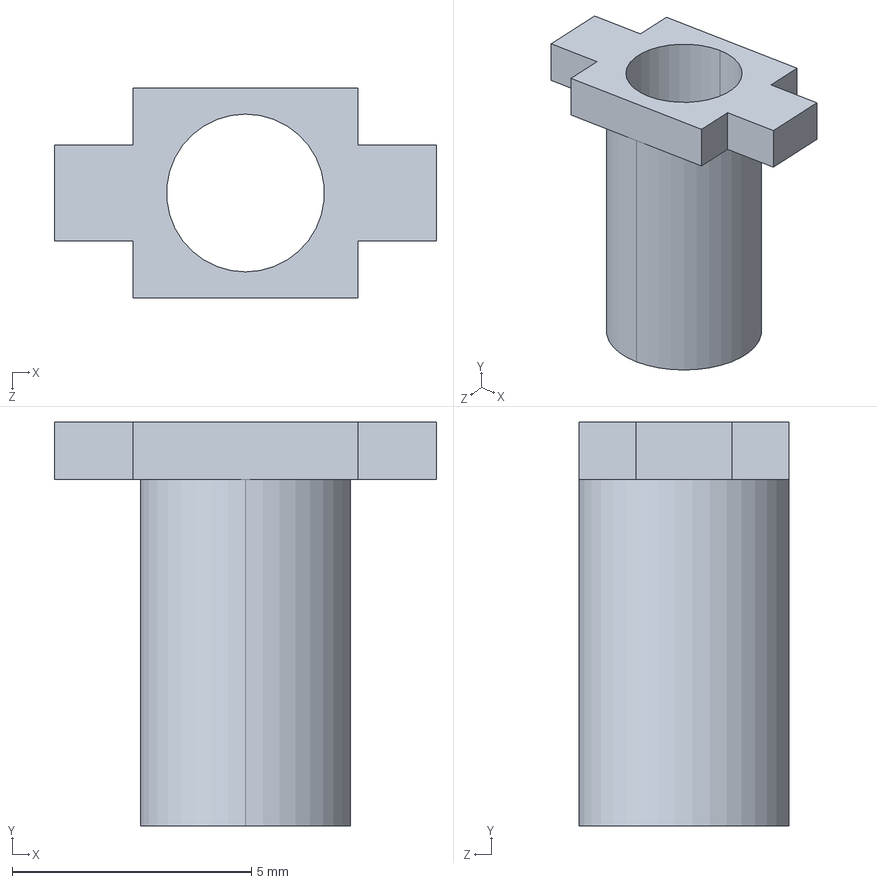
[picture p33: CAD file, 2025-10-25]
hw/assembly cad/USB-c/USB C Male Wire Tube.SLDPRT
8.00 x 8.45 x 4.40 mm

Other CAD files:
hw/assembly cad/Assem2.SLDASM
hw/assembly cad/Assembly.SLDASM
hw/assembly cad/Assembly2.SLDASM
hw/ECE445L_Lab7/models/ai_thinker_ESP8266-01.step
hw/ECE445L_Lab7/models/ti_TLV5618AIP.stp
hw/Part Libraries/models/ai_thinker_ESP8266-01.step
hw/Part Libraries/models/ti_TLV5618AIP.stp
hw/assembly cad/HC-SR04.SLDPRT
hw/assembly cad/STL files/enclosure.3mf
hw/assembly cad/STL files/enclosure.STL
hw/assembly cad/STL files/lid.3mf
hw/assembly cad/STL files/lid.STL
hw/assembly cad/STL files/lid2.STL
hw/assembly cad/STL files/tube lid.STL
hw/assembly cad/USB C Male Connector Board.step
hw/assembly cad/USB C Male Cover.STEP
hw/assembly cad/USB C Male Wire Tube.STEP
hw/assembly cad/USB-c/USB C Male Top Cover.SLDPRT
hw/assembly cad/enclosure.SLDPRT
hw/assembly cad/lid.SLDPRT
hw/assembly cad/model.step
hw/assembly cad/pcb.SLDASM
hw/assembly cad/pcb.step
hw/assembly cad/ping pong.SLDPRT
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

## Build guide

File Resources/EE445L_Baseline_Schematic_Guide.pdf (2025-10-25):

# EE445L – Fall 2021

Lab Baseline Schematic Guide: Rev 10-1-2021 | Page 1

### McDermott & Valvano

This semester we have decided to standardize the I/O Pin assignment to make remote debugging a little

### bit easier for the TAs. The standardized Signal and Port assignments are listed below:

PORT | SIGNAL NAME | TM4C PORT ASSIGNMENT | NOTES
Port-A[2] | ST7735_SCK | SSI0_SCK | SSI interface to the ST7735 LCD
Port-A[3] | ST7735_TFT_CS | SSI0_SS
Port-A[4] | ST7735_MISO | SSI0_MISO
Port-A[5] | ST7735_MOSI | SSI0_MOSI
Port-A[6] | ST7735_DC | GPIO
Port-A[7] | ST7735_RST | GPIO
PORT | SIGNAL NAME | TM4C PORT ASSIGNMENT | NOTES
Port-B[0] | ST7735_CARD_CS | GPIO | ST7735 SDCARD Chip Select
Port-B[1] | PB1 | GPIO | Used for simple speaker
Port-B[2] | PB2 | GPIO/I2C0_SCK | Primarily GPIO, can be used for I2C
Port-B[3] | PB3 | GPIO/I2C0_SDA
Port-B[4] | TACH2 | T1_CCP0 | Tach Input for Lab-10
Port-B[5] | PB5 | GPIO/AIN_11 | GPIO or Analog input
Port-B[6] | PWM | M0_PWM0 | PWM control for Lab-10
Port-B[7] | PB7 | GPIO/PWM1
PORT | SIGNAL NAME | TM4C PORT ASSIGNMENT | NOTES
Port-C[4] | UP | GPIO | Used for switches in Lab 3
Port-C[5] | RIGHT | GPIO
Port-C[6] | LEFT | GPIO
Port-C[7] | DOWN | GPIO
PORT | SIGNAL NAME | TM4C PORT ASSIGNMENT | NOTES
Port-D[0] | SSI1_SCK | SSI1_SCK | SCK to TLV5616 DAC
Port-D[1] | SSI1_FS | SSI1_FS | SS/FS to TLV5616 DAC
Port-D[2] | PD2 | AIN_5 | Used to monitor DAC_OUT
Port-D[3] | SSI1_MOSI | SSI1_MOSI | MOSI to TLV5616 DAC
Port-D[6] | PD6 | GPIO | Can be used as alternate UART Port
Port-D[7] | PD7 | GPIO
PORT | SIGNAL NAME | TM4C PORT ASSIGNMENT | NOTES
Port-E[0] | 8266_GPIO_2 | GPIO | Status signal 8266 WiFi
Port-E[1] | RSTB_8266 | GPIO | Reset signal to 8266 WiFi
Port-E[2] | AIN_1 | AIN1 | Used for Audio Input Lab-9
Port-E[3] | GPIO | GPIO
Port-E[4] | 8266_TX 8266_RX | U5_RX U5_TX | UART TXD/RXD to 8266 WiFi Port-E[5]
PORT | SIGNAL NAME | TM4C PORT ASSIGNMENT | NOTES
Port-F[0] | LAUNCHPAD_SW2 | RESERVED for Launchpad | Mode Switch
Port-F[1] | RED_LED | | Red LED on LaunchPad
Port-F[2] | BLUE_LED | | Blue LED on LaunchPad
Port-F[3] | GREEN_LED | | Green LED on LaunchPad
Port-F[4] | LAUNCHPAD_SW1 | | Mode Switch
The baseline schematic printout is shown on the next two pages. Use this as the starting point for Eagle

### Schematics

Lab Baseline Schematic Guide: Rev 10-1-2021 | Page 2

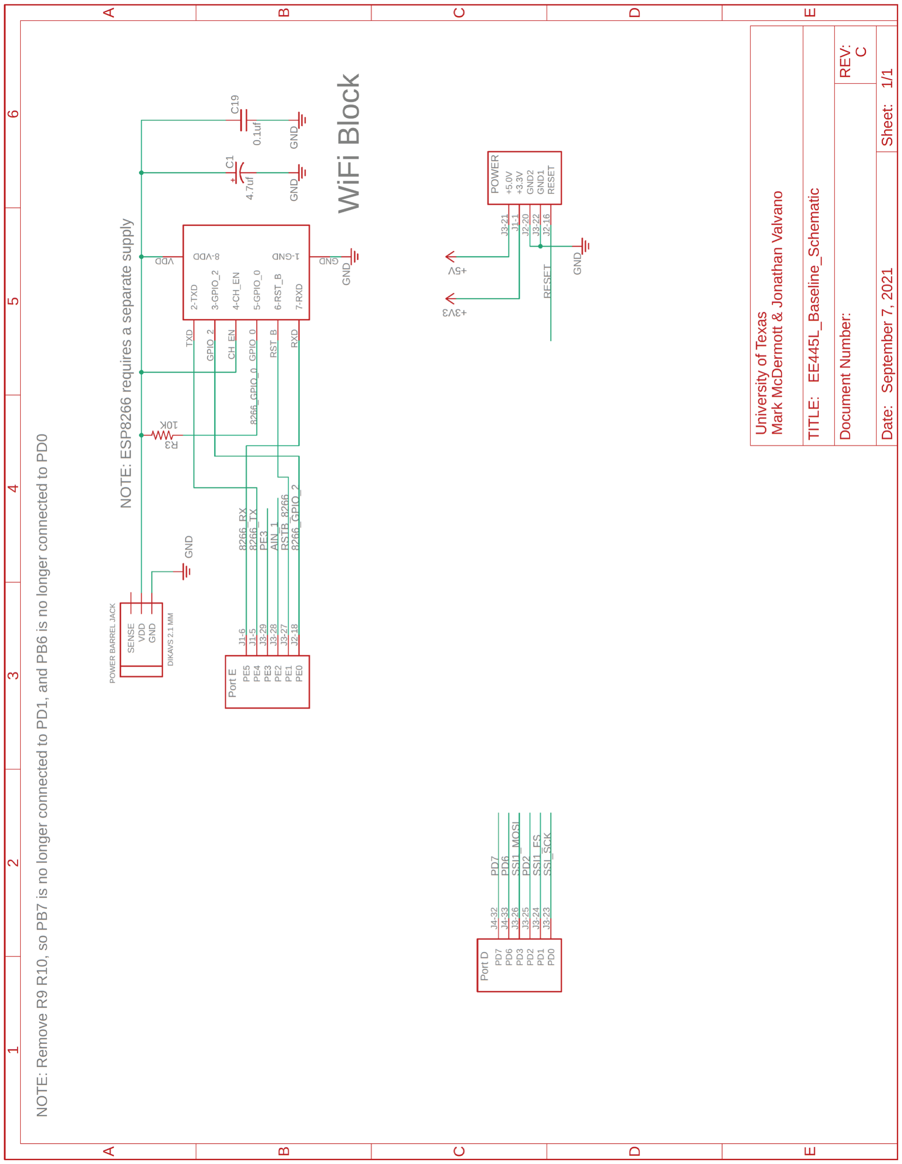
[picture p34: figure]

Lab Baseline Schematic Guide: Rev 10-1-2021 | Page 3

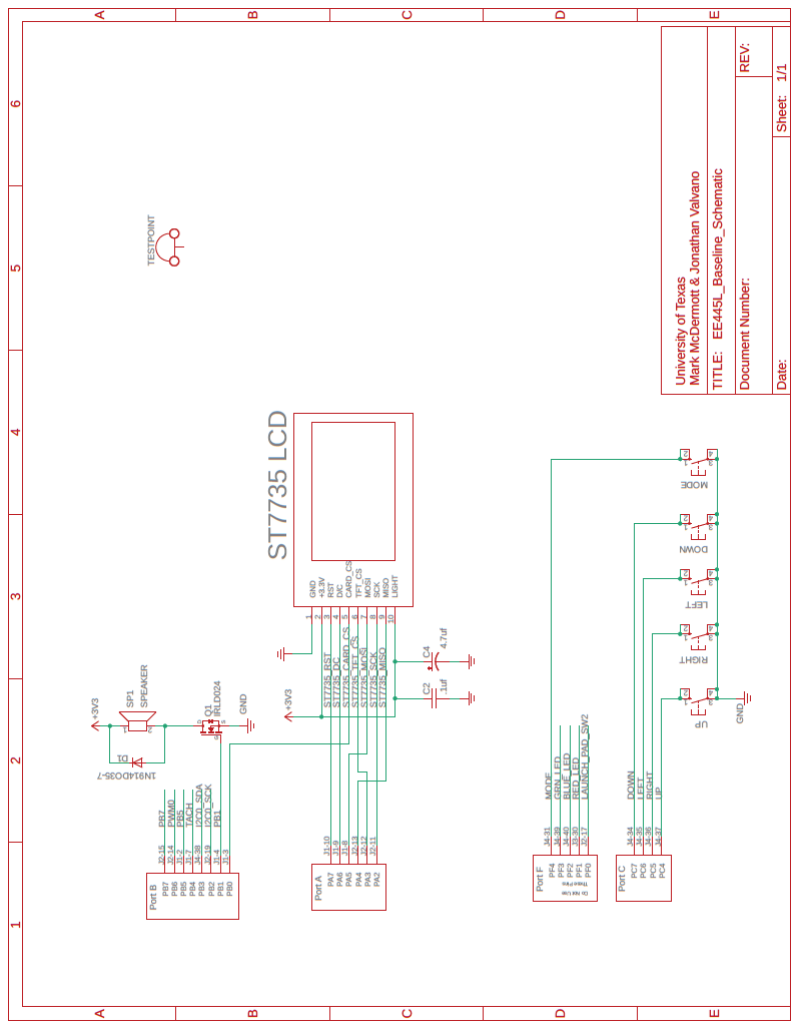
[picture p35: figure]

Lab Baseline Schematic Guide: Rev 10-1-2021 | Page 4

### PORT Initialization

Do not use this code without confirming that it does what you need it to do.

// ---------------------------------------------------------------------------//
// File name: Unified_Port_Init.c
//
// Author: | Mark McDermott
// Orig gen date: July 12, 2020
// Last update: August 17, 2020
//
// Description: This is the unified Port initialization routine 445L Labs
//
// Usage: | Call Lab_Brd_Port_Init () if you want to initialize all ports (preferred)
// | Call the individual port inits as needed.
//
// ---------------------------------------------------------------------------

#include "inc/tm4c123gh6pm.h"

#include "inc/Lab_Brd_Port_Init.h"

// --------------------------- | Port_Init | ------------------------------

void Lab_Brd_Port_Init(void){
Port_A_Init();
Port_B_Init();
Port_C_Init();
Port_D_Init();
Port_E_Init();
Port_F_Init();
}

// ----------------------------------------------------------------------------
// ---------------- | PORT A Initialization | --------------------------------
// ----------------------------------------------------------------------------//
// Port A drives the ST7735 LCD
//
// Backlight (pin 10) connected to +3.3 V
// MISO | (pin 9) connected to PA4
// SCK | (pin 8) connected to PA2 (SSI0Clk)
// MOSI | (pin 7) connected to PA5 (SSI0Tx)
// TFT_CS | (pin 6) connected to PA3 (SSI0Fss)
// CARD_CS | (pin 5) connected to PB0 (GPIO)
// Data/CMD (pin 4) connected to PA6 (GPIO)
// RESET | (pin 3) connected to PA7 (GPIO)
// VCC | (pin 2) connected to +3.3 V
// Gnd | (pin 1) connected to ground
//

void Port_A_Init(void){

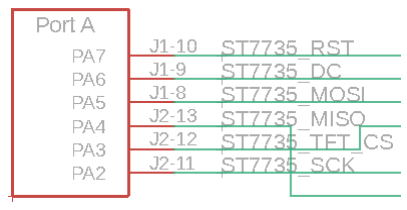
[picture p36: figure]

SYSCTL_RCGCSSI_R | |= 0x01; | // Activate SSI0
SYSCTL_RCGCGPIO_R | |= 0x01; | // Activate port A
while((SYSCTL_PRGPIO_R & 0x01)==0){}; | // allow time for clock to start
GPIO_PORTA_DIR_R | |= 0xC8; | // make PA3,6,7 out
GPIO_PORTA_AFSEL_R | &= ~0xC8; | // disable alt funct on PA3,6,7

Lab Baseline Schematic Guide: Rev 10-1-2021 | Page 5
GPIO_PORTA_DEN_R | |= 0xC8; | // enable digital I/O on PA3,6,7

// configure PA3,6,7 as GPIO
GPIO_PORTA_PCTL_R | = (GPIO_PORTA_PCTL_R
| & 0x00FF0FFF)
| + 0x00000000;
GPIO_PORTA_AMSEL_R | &= ~0xC8; | // disable analog functionality on PA3,6,7

// initialize SSI0
GPIO_PORTA_AFSEL_R | |= 0x2C; | // enable alt funct on PA2,3,5
GPIO_PORTA_DEN_R | |= 0x2C; | // enable digital I/O on PA2,3,5

// configure PA2,3,5 as SSI
GPIO_PORTA_PCTL_R | = (GPIO_PORTA_PCTL_R
| & 0xFF0F00FF)
| + 0x00202200;
GPIO_PORTA_AMSEL_R | &= ~0x2C; | // disable analog functionality on PA2,3,5
SSI0_CR1_R | &= ~SSI_CR1_SSE; | // disable SSI
SSI0_CR1_R | &= ~SSI_CR1_MS; | // master mode

// configure for system clock/PLL baud clock source
SSI0_CC_R | = (SSI0_CC_R&~SSI_CC_CS_M)
| + SSI_CC_CS_SYSPLL;

// clock divider for 8 MHz SSIClk (80 MHz PLL/24) // SysClk/(CPSDVSR*(1+SCR))
// 80/(10*(1+0)) = 8 MHz (slower than 4 MHz)
SSI0_CPSR_R | = (SSI0_CPSR_R
&~SSI_CPSR_CPSDVSR_M)
| + 10; | // must be even number

// SCR = 0 (8 Mbps data rate)
// SPH = 0
// SPO = 0
SSI0_CR0_R | &= ~(SSI_CR0_SCR_M
| | SSI_CR0_SPH
| | SSI_CR0_SPO);

// FRF = Freescale format
SSI0_CR0_R | = (SSI0_CR0_R
| &~SSI_CR0_FRF_M)
| + SSI_CR0_FRF_MOTO;

// DSS = 8-bit data
SSI0_CR0_R | = (SSI0_CR0_R
| &~SSI_CR0_DSS_M)
| + SSI_CR0_DSS_8;
// enable SSI
SSI0_CR1_R | |= SSI_CR1_SSE;

}

Lab Baseline Schematic Guide: Rev 10-1-2021 | Page 6

// ----------------------------------------------------------------------------
// ---------------- | PORT B Initialization | --------------------------------
// ----------------------------------------------------------------------------
//
// PB7 = GPIO/M0PWM1
// PB6 = PWM Output to Motor (M0PWM0)
// PB5 = GPIO/AIN11
// PB4 = Timer Capture input (TACH) // PB3 = GPIO/I2C_SDA
// PB2 = GPIO/I2C0_SCL
// PB1 = GPIO
// PB0 = ST7735 Card CS

void Port_B_Init(void){

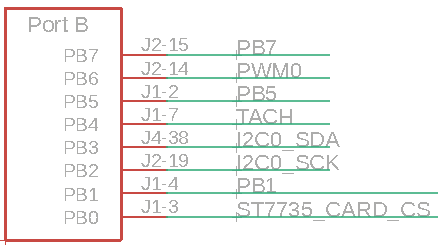
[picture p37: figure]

SYSCTL_RCGCPWM_R | |= 0x01; | // activate PWM0
SYSCTL_RCGCGPIO_R | |= 0x02; | // activate port B
while((SYSCTL_PRGPIO_R & 0x02) == 0){}; | // Wait

// --------------- Initialize PB7 as M0PWM1 -----------------------

GPIO_PORTB_AFSEL_R | |= 0x80; | // enable alt funct on PB7
GPIO_PORTB_PCTL_R | &= ~0xF0000000; | // configure PB7 as M0PWM1
GPIO_PORTB_PCTL_R | |= 0x40000000;
GPIO_PORTB_AMSEL_R | &= ~0x80; | // disable analog functionality on PB7
GPIO_PORTB_DEN_R | |= 0x80; | // enable digital I/O on PB7

// --------------- Initialize PB6 as M0PWM0 -----------------------
GPIO_PORTB_AFSEL_R | |= 0x40; | // enable alt funct on PB6
GPIO_PORTB_PCTL_R | &= ~0x0F000000; | // configure PB6 as PWM0
GPIO_PORTB_PCTL_R | |= 0x04000000;
GPIO_PORTB_AMSEL_R | &= ~0x40; | // disable analog functionality on PB6
GPIO_PORTB_DEN_R | |= 0x40; | // enable digital I/O on PB6

// --------------- Initialize PB5 as AIN11 -----------------------
GPIO_PORTB_DIR_R | &= ~0x20; | // make PB5 input
GPIO_PORTB_AFSEL_R | |= 0x20; | // enable alternate function on PB5
GPIO_PORTB_DEN_R | &= ~0x20; | // disable digital I/O on PB5
GPIO_PORTB_AMSEL_R | |= 0x20; | // enable analog functionality on PB5

// ----------------- Initialize PB4 as Timer Capture input (T1CCP0) ---------
GPIO_PORTB_DIR_R | &= ~0x10; | // make PB4 input
GPIO_PORTB_AFSEL_R | |= 0x10; | // enable alt funct on PB4
GPIO_PORTB_DEN_R | |= 0x10; | // enable digital I/O on PB4
| | // configure PB4 (T1CCP0)
GPIO_PORTB_PCTL_R | = (GPIO_PORTB_PCTL_R
| & 0xFFF0FFFF)
| + 0x00070000;
GPIO_PORTB_AMSEL_R | &= ~0x10; | // disable analog functionality on PB4

// ----------------- Initialize PB3-0 as GPIO ---------
GPIO_PORTB_PCTL_R | &= ~0x0000FFFF; | // GPIO
GPIO_PORTB_DIR_R | |= 0x0F; | // make PB3-0 out
GPIO_PORTB_AFSEL_R | &= ~0x0F; | // regular port function
GPIO_PORTB_DEN_R | |= 0x0F; | // enable digital I/O on PB3-0
GPIO_PORTB_AMSEL_R | &= ~0x0F; | // disable analog functionality on PB3-0
}

Lab Baseline Schematic Guide: Rev 10-1-2021 | Page 7

// ----------------------------------------------------------------------------
// ---------------- | PORT C Initialization | --------------------------------
// ----------------------------------------------------------------------------
//
// PC4 = UP switch
// PC5 = RIGHT switch
// PC6 = LEFT switch
// PC7 = DOWN switch
//

void Port_C_Init(void){

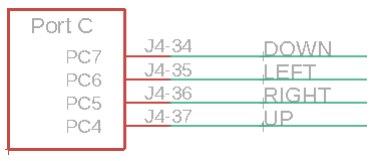
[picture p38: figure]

SYSCTL_RCGCGPIO_R | |= 0x04; | // Activate clock for Port C
while((SYSCTL_PRGPIO_R & 0x04) != 0x04){}; // Allow time for clock to start
GPIO_PORTC_PCTL_R | &= ~0xFFFF0000; | // regular GPIO
GPIO_PORTC_AMSEL_R | &= ~0xF0; | // disable analog function
GPIO_PORTC_DIR_R | &= ~0xF0; | // inputs on PC7-PC4
GPIO_PORTC_AFSEL_R | &= ~0xF0; | // regular port function
GPIO_PORTC_DEN_R | |= 0xF0; | // enable digital port
}

Lab Baseline Schematic Guide: Rev 10-1-2021 | Page 8

// ----------------------------------------------------------------------------
// ---------------- | PORT D Initialization | --------------------------------
// ----------------------------------------------------------------------------
//
// PD7 = GPIO/U2TX
// PD6 = GPIO/U2RX
// PD5 = Reserved for LaunchPad // PD4 = Reserved for Launchpad // PD3 = SSI1_MOSI (to TLV5616) // PD2 = AIN5
// PD1 = SSI1_FS/CS (to TLV5616) // PD0 = SSI1_SCK (to TLV5616)

void Port_D_Init(void){

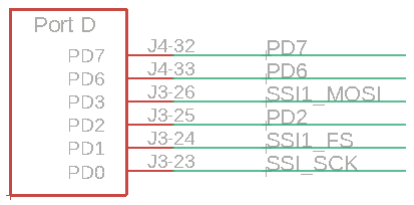
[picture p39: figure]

SYSCTL_RCGCGPIO_R | |= 0x08; | // activate port D
while((SYSCTL_PRGPIO_R & 0x08)==0){}; | // allow time for clock to stabilize

// --------------- Initialize PB7 as U2TX, PB6 as U2RX -----------------------

GPIO_PORTD_LOCK_R | = 0x4C4F434B; | // unlock REQUIRED for PD7
GPIO_PORTD_CR_R | |= 0xC0; | // commit PD6, PD7
GPIO_PORTD_AMSEL_R | &= ~0xC0; | // disable analog functionality on PD6, PD7
GPIO_PORTD_AFSEL_R | |= 0xC0; | // enable alternate function on PD6, PD7
GPIO_PORTD_DEN_R | |= 0xC0; | // enable digital on PD6, PD7 (PD6 is U2RX, PD7 is
U2TX)
GPIO_PORTD_PCTL_R =(GPIO_PORTD_PCTL_R
& 0x00FFFFFF)
| 0x11000000; // configure PD6, PD7 as UART

// --------------- Initialize PD2 as AIN5 ----------------------------------

GPIO_PORTD_DIR_R | &= ~0x04; | // make PD2 input
GPIO_PORTD_AFSEL_R | |= 0x04; | // enable alternate function on PD2
GPIO_PORTD_DEN_R | &= ~0x04; | // disable digital I/O on PD2
GPIO_PORTD_AMSEL_R | |= 0x04; | // enable analog functionality on PD2
// --------------- Initialize PD3,1,0 as SSI1 MOSI, FS & SCK ----------------
GPIO_PORTD_AMSEL_R | &= ~0x0B; | // disable analog functionality on PD
GPIO_PORTD_AFSEL_R | |= 0x0B; | // enable alt funct on PD3,1,0
GPIO_PORTD_DEN_R | |= 0x0B; | // enable digital I/O on PD3,1,0
GPIO_PORTD_PCTL_R | = (GPIO_PORTD_PCTL_R
& 0xFFFF0F00)
+ 0x00002022;
}

Lab Baseline Schematic Guide: Rev 10-1-2021 | Page 9

// ----------------------------------------------------------------------------
// ---------------- | PORT E Initialization | --------------------------------
// ----------------------------------------------------------------------------
//
// PE5 = 8266_RX (U5TX)
// PE4 = 8266_TX (U5RX)
// PE3 = GPIO
// PE2 = AIN_1 (Audio Input) // PE1 = 8266_8266
// PE0 = 8266_ GPIO_2

void Port_E_Init(void){

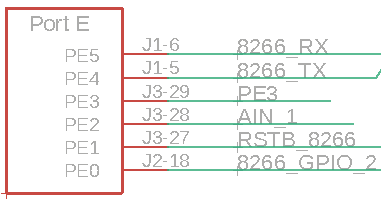
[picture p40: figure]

SYSCTL_RCGCGPIO_R | |= 0x10; | // activate port E
while((SYSCTL_PRGPIO_R & 0x10)==0){};

// --------------- Initialize PE5 as U5TX, PE4 as U5RX -----------------------

GPIO_PORTE_AFSEL_R | |= 0x30; | // enable alt funct on PE5-4
GPIO_PORTE_DEN_R | |= 0x30; | // enable digital I/O on PE5-4
| | // configure PE5-4 as UART
GPIO_PORTE_PCTL_R | = (GPIO_PORTE_PCTL_R
| & 0xFF00FFFF)
| + 0x00110000;
GPIO_PORTE_AMSEL_R | &= ~0x30; | // disable analog functionality on PE
// --------------- Initialize PE3,1,0 as GPIO ---------------------------------
GPIO_PORTE_DIR_R | |= 0x0A; | // output digital I/O on PE3,1
GPIO_PORTE_DIR_R | &= ~0x01; | // input digital I/O on PE0
GPIO_PORTE_AMSEL_R | &= ~0x0B; | // disable analog functionality on PE3,1,0
GPIO_PORTE_AFSEL_R | &= ~0x0B; | // disable alt funct on PE3,1,0
GPIO_PORTE_DEN_R | |= 0x0B; | // enable digital I/O on PE3,1,0
GPIO_PORTE_PCTL_R | = (GPIO_PORTE_PCTL_R
| & 0xFFFF0F00);
// --------------- Initialize PE2 as AIN1 ---------------------------------
GPIO_PORTE_DIR_R | &= ~0x04; | // make PE2 input
GPIO_PORTE_AFSEL_R | |= 0x04; | // enable alternate function on PE2
GPIO_PORTE_DEN_R | &= ~0x04; | // disable digital I/O on PE2
GPIO_PORTE_AMSEL_R | |= 0x04; | // enable analog functionality on PE2
}

Lab Baseline Schematic Guide: Rev 10-1-2021 | Page 10

// ----------------------------------------------------------------------------
// ---------------- | PORT F Initialization | --------------------------------
// ----------------------------------------------------------------------------//
// LaunchPad Pin Assignments
// PF4 = SW1
// PF3 = GREEN_LED
// PF2 = BLUE_LED
// PF1 = RED_LED
// PF0 = SW2

void Port_F_Init(void){

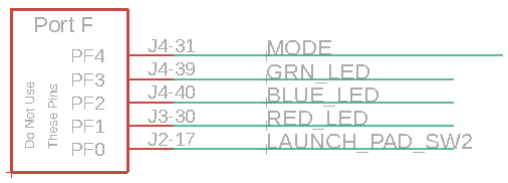
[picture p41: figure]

SYSCTL_RCGCGPIO_R | |= 0x00000020; | // activate clock for Port F
while((SYSCTL_PRGPIO_R & 0x20)==0){}; | // allow time for clock to stabilize
GPIO_PORTF_LOCK_R | = 0x4C4F434B; | // unlock GPIO Port F
GPIO_PORTF_CR_R | = 0x1F; | // allow changes to PF4-0
GPIO_PORTF_AMSEL_R | = 0x00; | // disable analog on PF
GPIO_PORTF_PCTL_R | = 0x00000000; | // PCTL GPIO on PF4-0
GPIO_PORTF_DIR_R | = 0x0E; | // PF4,PF0 in, PF3-1 out
GPIO_PORTF_AFSEL_R | = 0x00; | // disable alt function on PF7-0
GPIO_PORTF_PUR_R | = 0x11; | // enable pull-up on PF0 and PF4
GPIO_PORTF_DEN_R | = 0x1F; | // enable digital I/O on PF4-0
}

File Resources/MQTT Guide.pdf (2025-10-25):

## Contents

Lab 4 MQTT Writeup | 2

The Mobile App makes a change to thermostat temperature or

1

## Lab 4 MQTT Writeup

Key Aspects of MQTT

MQTT (Message Queuing Telemetry Transport), is a lightweight messaging protocol designed for low-bandwidth, high-latency, and unreliable networks. Developed in 1999 by IBM, MQTT is now a widely used open standard. MQTT is useful as it can:

- Organize data at the protocol level
- Cordinate actions between IOT devices
- Allow easy centralization of data to user-facing dashboards
- Send connected clients only the data they need
- Ensure a Quality Of Service (QOS) of data sent by clients

MQTT topology and the Publish/Subscribe Model:

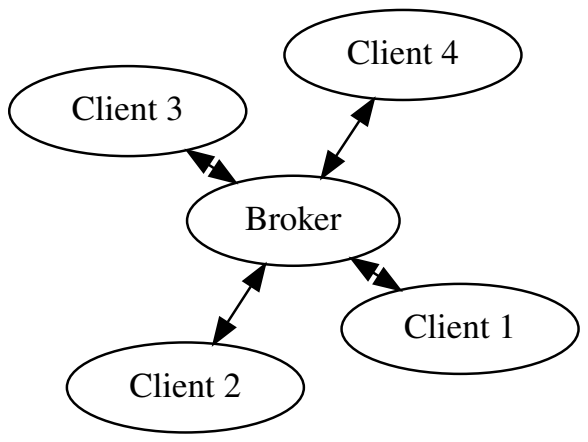
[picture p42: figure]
Broker; Client 1; Client 2; Client 3; Client 4

Figure 1: MQTT Client-Broker topology

MQTT includes ONLY broker to client/client to broker comunications. MQTT networks have one broker which facilitates comunication between many clients.

MQTT uses a Publish/Subscribe Model. In this model, data movement is controled by topics. Clients decide what data they recive, by deciding what topics they subscribe to. Clients can influence where data is sent by choosing what topic they attach to the data they publish. The messages sent and recived allways consist of a topic & data.

Although the broker is responsible for relaying data, it has no discresion to decide where data goes. The broker will relay a published message from any client to all clients that are subscribed to the topic of the message.

2

Topic Naming scheme:

An MQTT topic is a hierarchical string identifier that categorizes messages being published/subscribed to within the MQTT system. Topics are represented as strings and are organized hierarchically using forward slashes (‘/’). For example, a topic could be

"sensors/temperature/EER/floor1/embeddedlab."

or

"EER/floor1/embeddedlab/temperature"

How topics are defined are up to you. As long as they follow the typical hierarchical format.

Example of MQTT Communication

Here is an example of a typical MQTT communication between clients and how the broker routes it.

1. An MQTT client publishes a message to a specific topic on the MQTT broker.
2. The MQTT broker receives the published message and examines the topic.
3. The broker checks its subscription database to determine which MQTT client have subscribed to that topic.
4. The broker forwards the message to all subscribed clients
5. Subscribed MQTT clients receive the message and can take action based on its content.

Now lets imagine a scenario where we have a IoT setup in the EER. We have a three sensors which are their very own internet conected devices located in the EER. We have a temperature sensor in the 445L lab room, a thermostat located in the 319K room (let’s imagine the thermostat controls the A.C for the entirety of floor 1), and a faculty member has a mobile app that allows him to control the thermostat or see the readings from the sensors.

Here we have three clients:

- 445L Temperature Sensor
– Can read temperature in the 445L room
- 319K Lab Thermostat
– Connected via wire to the A.C, can control the A.C for the entirety of floor 1.
– Has its own temperature sensor that allows it to read the temperature in the room it is in (the 319K lab in this case)

3

– Has a temperature the thermostat can be set too. If the temperature in any of the rooms dip/rise above this temperature. The A.C is enabled to heat/cool
– Has a mode for the A.C. The A.C can either be off, set to cool, or set to heat.
– Can interface with external temperature sensors (such as the 445L temperature sensor)
– This closely resembles popular IoT thermostats such as the Nest or Ecobee
- Mobile App
– Allows you to control the thermostat (mode, set temperature)
– Read the temperature readings across all temperature sensors

All of these clients are connected to one central server (The MQTT Broker) to faciliate communication. This server could be for examples McDermott MQTT server in his office, or a public/cloud based MQTT Server.

Figure 2: Client-Broker setup of the Example

Now lets try to analyze what information each client provides, and what information each client would want from another client.

- 445L Temperature Sensor
– Reads the 445l lab room temperature, publishes it.
- 319K Lab Thermostat
– Reads the temperature in the 319K room, can act on this reading (enable the A.C for floor 1). Can also publish it (for the mobile app) – Is interested in the temperature in the 445L room, can act on this reading (enable the A.C for floor 1)
– Has a temperature that can be set to enable cooling/heat (acting on this data) It can publish this temperature (for the mobile app), and it can also have this changed externally (from the mobile app)
– Has a A.C mode (off/cool/heat). It acts on this mode (enable the A.C for cool/hot if the outside temperature changes). It can publish this data (so the mobile app knows the current A.C mode), it can also have this changed externally (from the mobile app)
- Mobile App
– Can set the A.C mode from the mobile app. Changes to this can be made from app or thermostate

4

– Can set the thermostat temperature. Changes can be made from app or thermostat.
– Can read all temperature sensor readings.

From this lets define the following topics, and these publishers and subscribers

- /EER/floor1/445Lab/temperature
- Publishers:
- 445L Temperature Sensor
- Subscribers:
- 319K Thermostat
- Mobile App
- /EER/floor1/319KLab/temperature
- Publishers:
- 319K Thermostat
- Subscribers:
- Mobile App
- /EER/floor1/thermostat/set_temp
- Publishers:
- 319K Thermostat
- Mobile App
- Subscribers:
- 319K Thermostat
- Mobile App
- /EER/floor1/thermostat/mode
- Publishers:
- 319K Thermostat
- Mobile App
- Subscribers:
- 319K Thermostat
- Mobile App

The scenario where 445L Lab Temp Changes

If the 445L lab room temperature changes. The sensor publishes to its topic its payload.

5

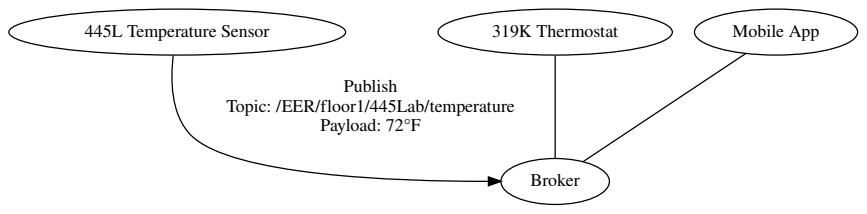
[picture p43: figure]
Broker; 445L Temperature Sensor; Publish Topic: /EER/floor1/445Lab/temperature Payload: 72°F; 319K Thermostat; Mobile App

Figure 3: 445L Temperature Sensor publishes change

The thermostat, and mobile app are subscribers and therefore notified.

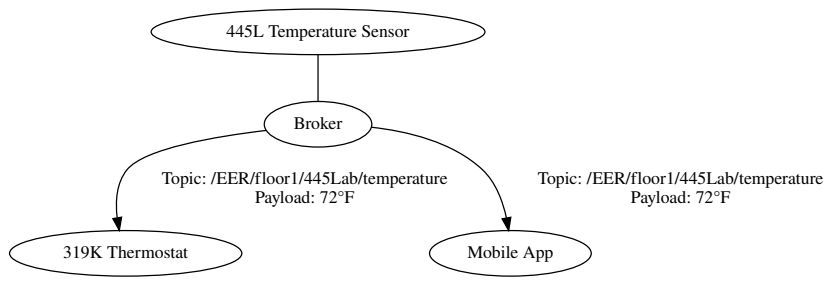
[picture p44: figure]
Broker; 319K Thermostat; Topic: /EER/floor1/445Lab/temperature Payload: 72°F; Mobile App; 445L Temperature Sensor

Figure 4: Subscribers are notified

The thermostat could act on this change. For example if the temperature 72°F exceeds/below the set temperature, it could enable the A.C. The mobile app also now has up-to date sensor reading.

The scenario where 319K Lab temp changes.

The thermostat has it’s own temperature sensor measuring the temperature of the 319K room. The thermostat can act this temperature (enable the A.C for example). But the mobile app also wants to be up-to date regarding all temperature readings.

6

Figure 5: Thermostat Temperature Sensor publishes change

The mobile app is subscribed to the all temperature readings, including the

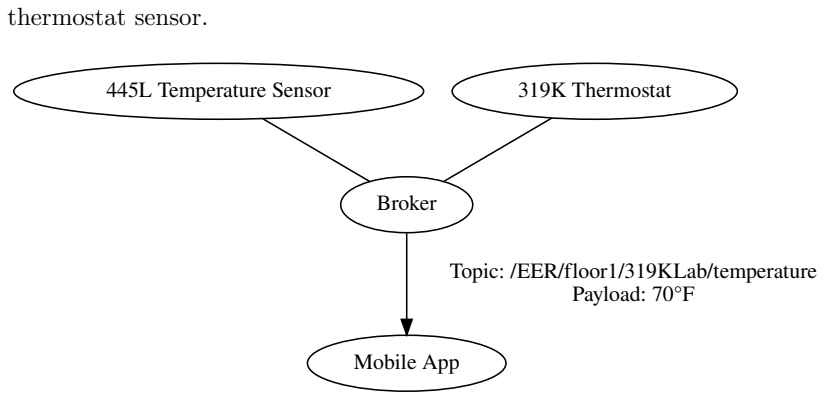
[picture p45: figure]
thermostat sensor.; Broker; Mobile App; Topic: /EER/floor1/319KLab/temperature Payload: 70°F; 445L Temperature Sensor; 319K Thermostat

Figure 6: Subscribers are notified

Thermostat has a change in set temperature or mode.

If you were to change the set temperature on the thermostat.

Figure 7: Thermostat Set Temp changes

The mobile app will be notified.

7

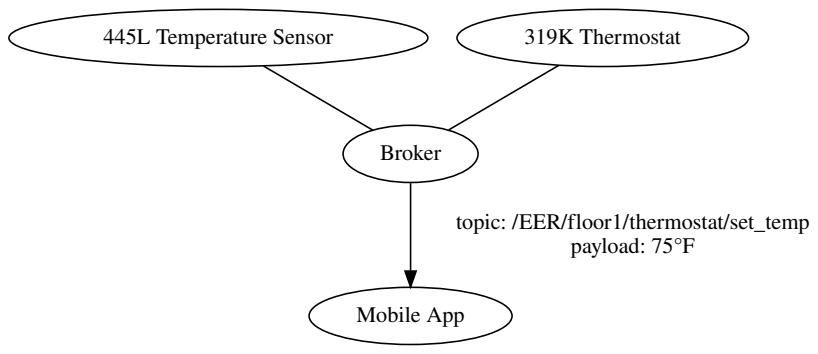
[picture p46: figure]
Broker; Mobile App; topic: /EER/floor1/thermostat/set_temp payload: 75°F; 445L Temperature Sensor; 319K Thermostat

Figure 8: Subscribers are notified

Similarily if you were to change the mode from “heat” to “cool” on the thermostat

Figure 9: Thermostat Set Temp changes

The mobile app will be notified.

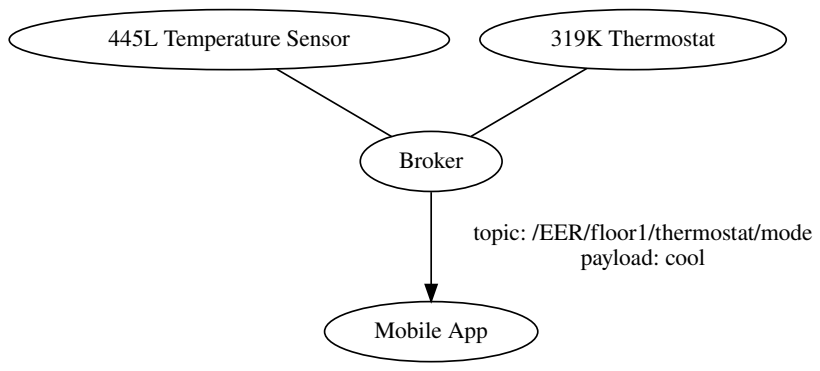
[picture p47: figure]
Broker; Mobile App; topic: /EER/floor1/thermostat/mode payload: cool; 445L Temperature Sensor; 319K Thermostat

Figure 10: Subscribers are notified

8

The Mobile App makes a change to thermostat temperature or mode

If we want to change the set temperature of the thermostat from the mobile app.

Figure 11: Thermostat Set Temp changes from Mobile App

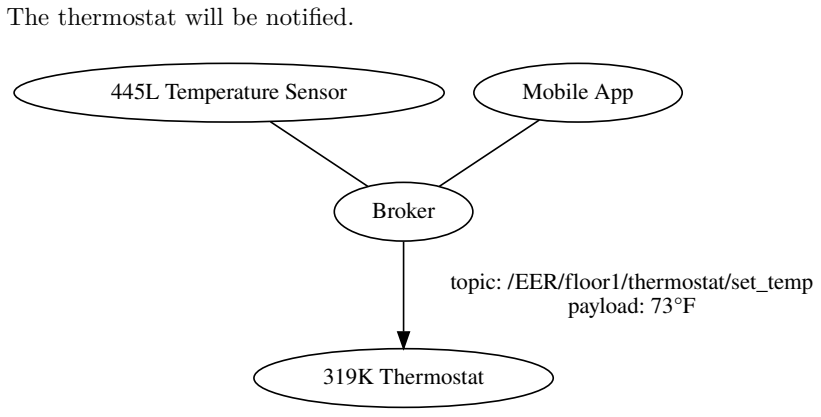
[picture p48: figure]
The thermostat will be notified.; Broker; 319K Thermostat; topic: /EER/floor1/thermostat/set_temp payload: 73°F; 445L Temperature Sensor; Mobile App

Figure 12: Subscribers are notified

Similarily if we want to turn off the A.C from the mobile app.

Figure 13: Thermostat Mode changes from Mobile App

The thermostat will be notified.

9

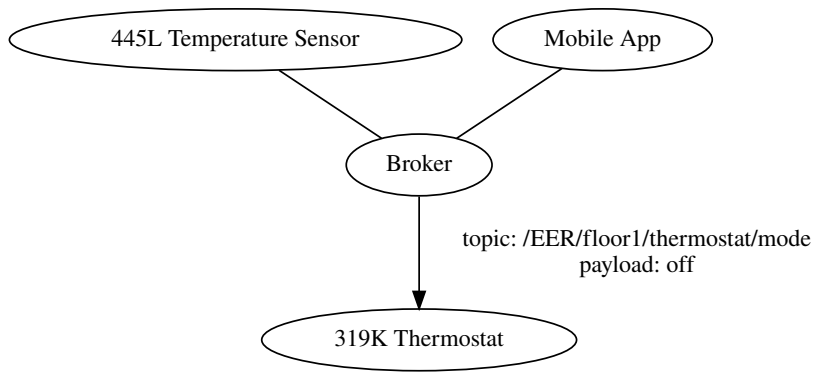
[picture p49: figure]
Broker; 319K Thermostat; topic: /EER/floor1/thermostat/mode payload: off; 445L Temperature Sensor; Mobile App

Figure 14: Subscribers are notified

How to approach Lab 4

From the perspective of the lab we have two clients:

- Your Alarm Clock
- The web dashboard

and a broker (the free broker service we are using called emqx.io).

From the perspective of the free broker service however, it has your alarm clock and web dashboard as a client. As well as the alarm clock and web dashboard of everyone else in the class (and anyone else using the service). So when you define your topics make sure the topic string is unique. For example if everyone used the same topic, lets say “alarm/current_time”, you would be able to change the time of everyones alarm clock. So to make unique topic names, your topic should start with your eid, ex. “eid123/alarm/current_time”.

Here is how we reccomend approaching this lab to avoid stress and headaches. First things first, don’t try integrating lab3 right away, instead get topics working.

Using the starter code, do the following.

1. ESP Bring up, the ESP8266 should be able to connect to a network and to the broker. This should be done in prep. Come to your TA’s if you were unable to do this.
2. Define your topics, and the subscriber/publisher relationships.
3. Have both of you open the web dashboard. Have one person subscribe to a topic, and have the other publish to the topic. The subscriber should be able to receive a message when this happens.
4. Modify your TM4C starter code so you can communicate with the ESP. The TM4C communicates with the ESP over UART. You can observe what

10 is being sent to the ESP via USB-Serial between your PC and the TM4C using a serial terminal.
5. Test, can you publish to a topic from the TM4C, do you see this change reflected on the web dashboard?
6. Test, can you publish to a topic from the web dashboard, do you see this change reflected on the TM4C?
7. Now that you can publish/subscribe to topics. Now integrate your Lab 3 Code.

If you need any help, please email us or come to our office hours.

11

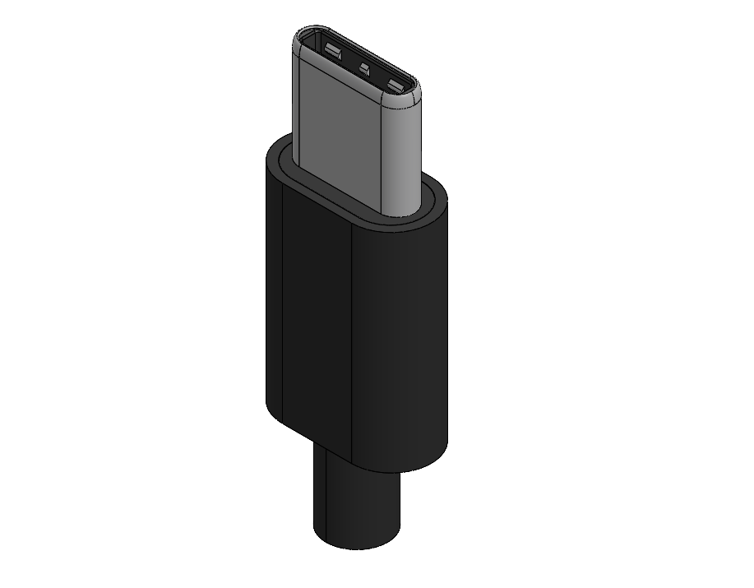
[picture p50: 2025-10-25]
hw/assembly cad/USB C Male.png

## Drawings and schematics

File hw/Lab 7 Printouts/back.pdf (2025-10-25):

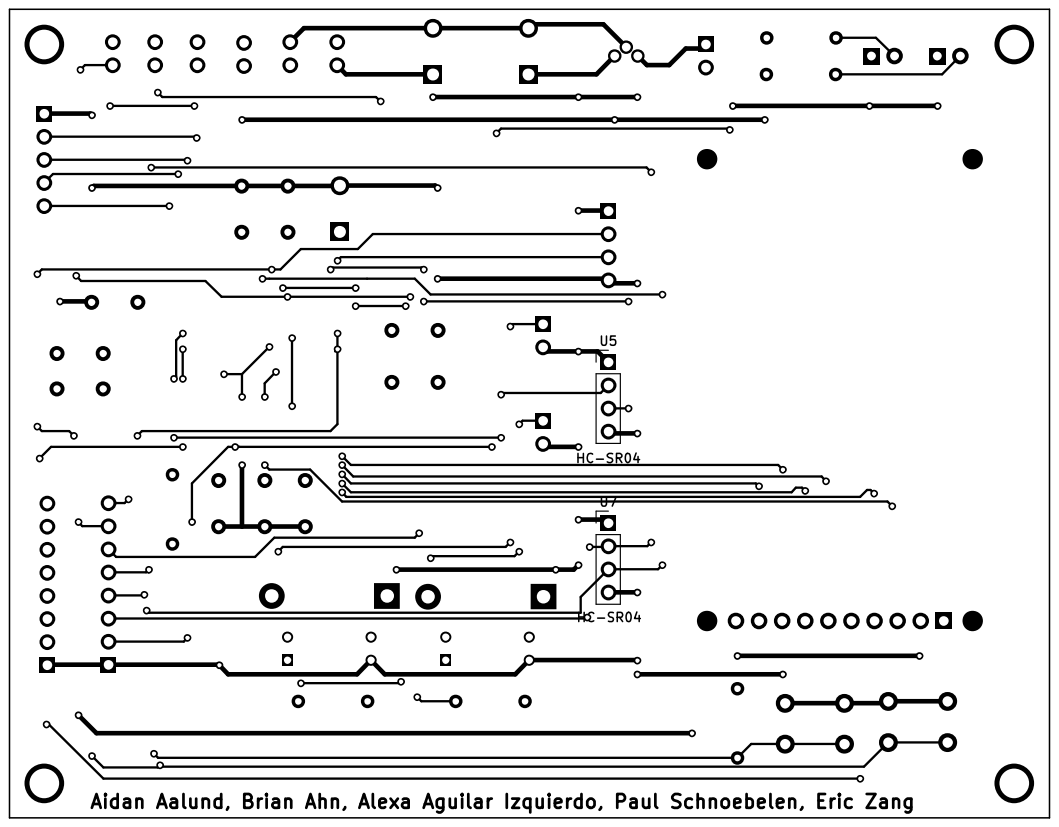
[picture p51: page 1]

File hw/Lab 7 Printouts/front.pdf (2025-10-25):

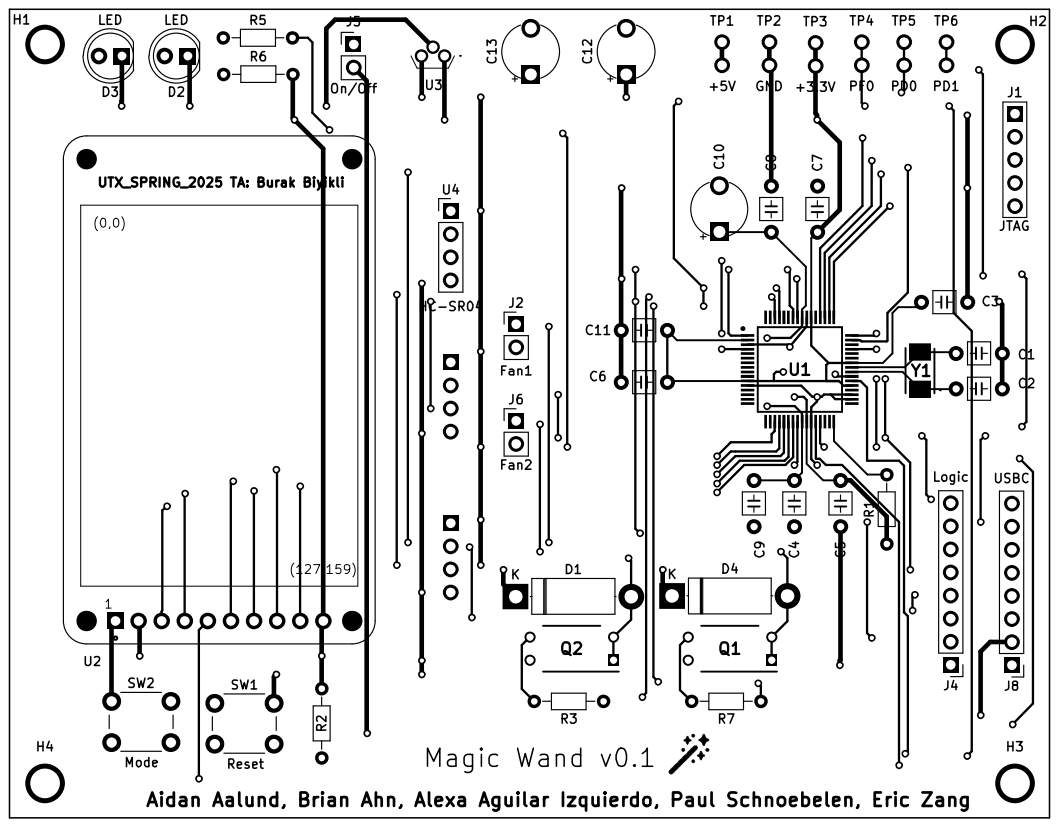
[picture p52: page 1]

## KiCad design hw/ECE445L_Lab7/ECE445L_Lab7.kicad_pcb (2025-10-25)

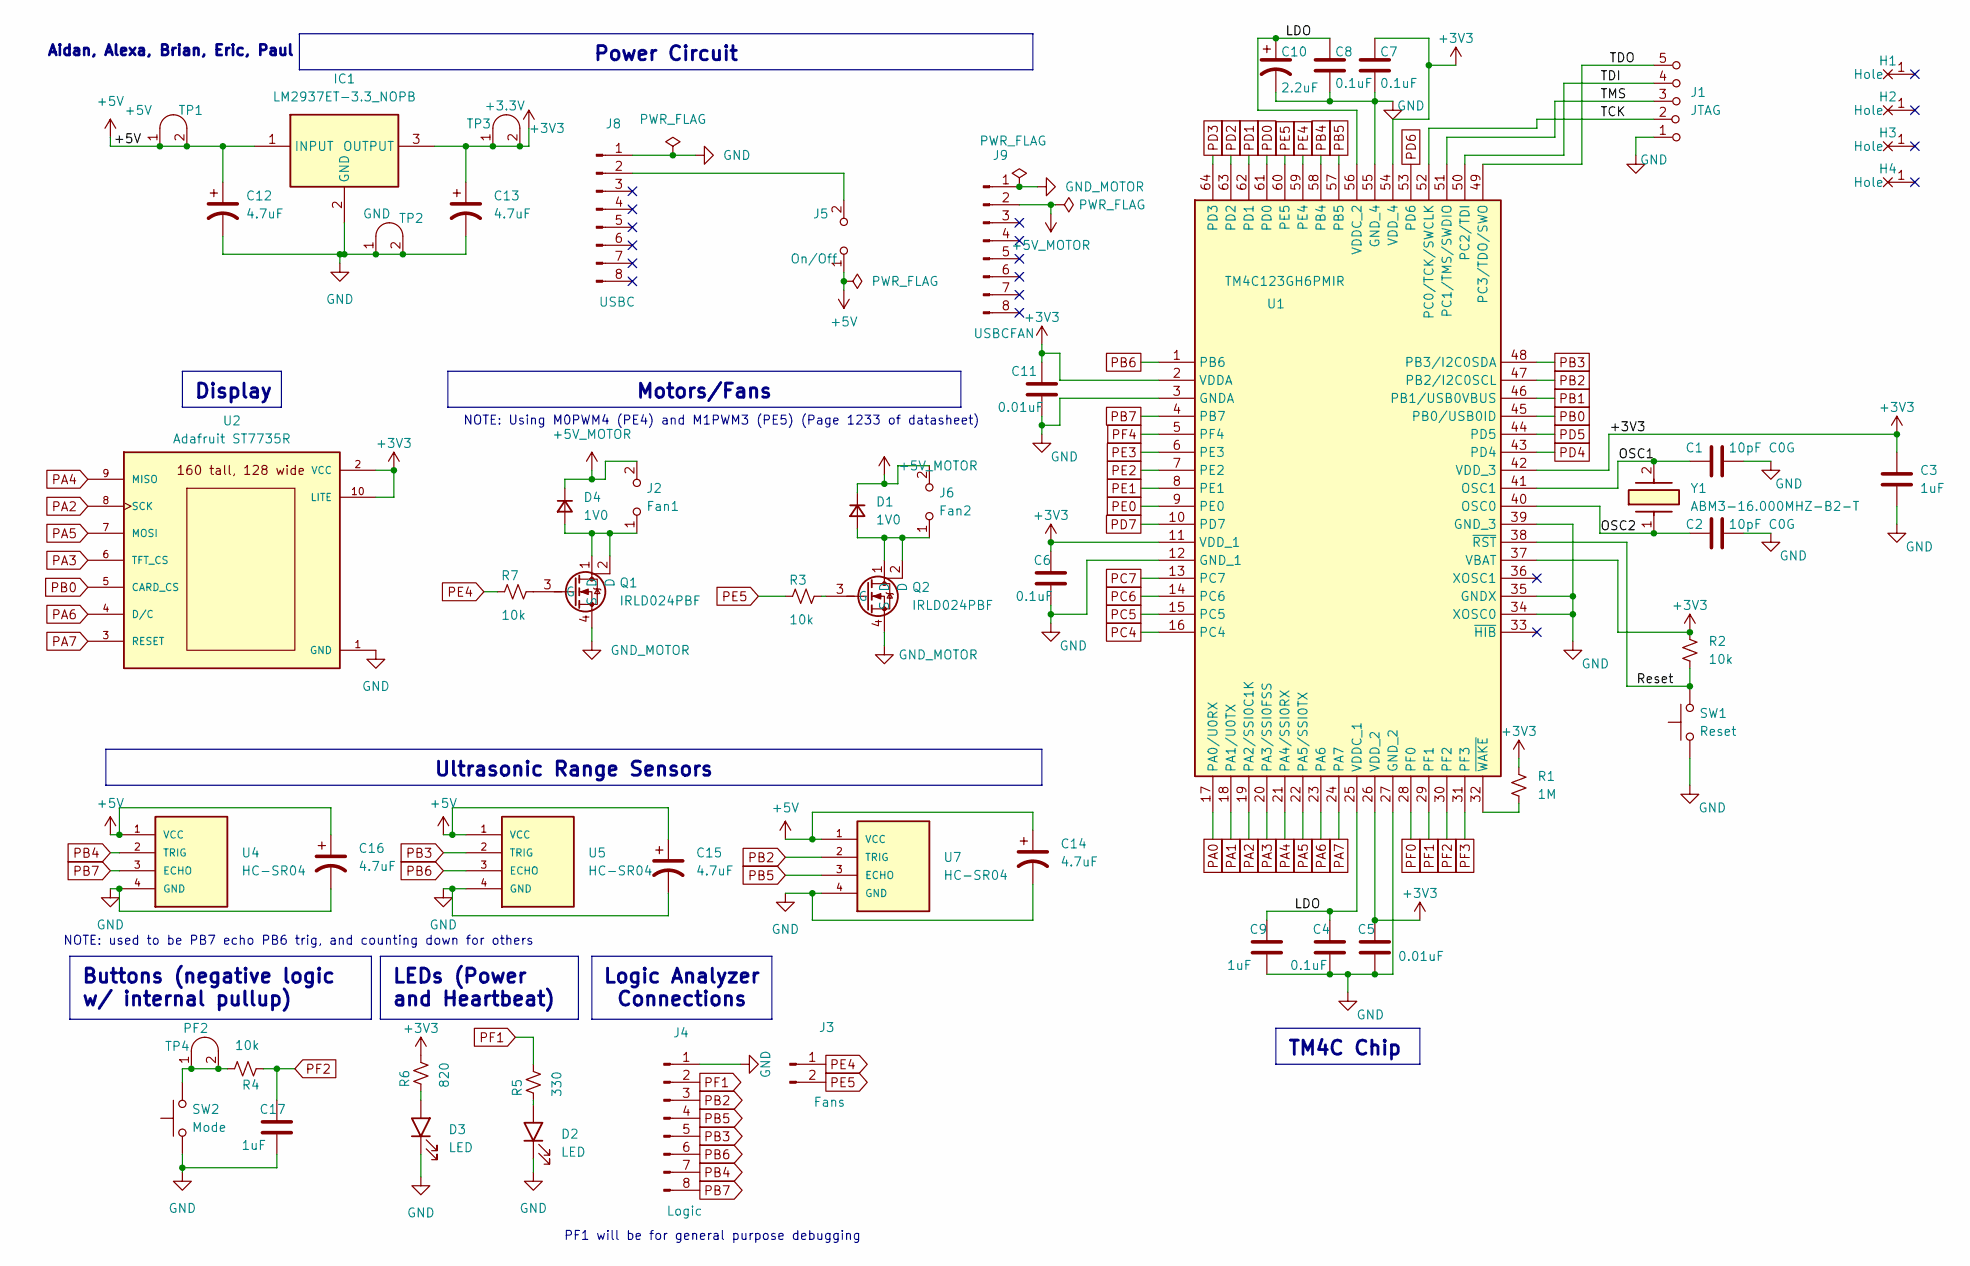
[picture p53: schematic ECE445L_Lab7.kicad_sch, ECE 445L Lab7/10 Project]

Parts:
C1, C2: 10pF C0G; C_Axial_200mil
C3, C9, C17: 1uF; C_Axial_200mil
C4, C6, C7, C8: 0.1uF; C_Axial_200mil
C5, C11: 0.01uF; C_Axial_200mil
C10: 2.2uF; CP_Radial_Tantal200mil
C12, C13, C14, C15, C16: 4.7uF; CP_Radial_Tantal200mil
D1, D4: 1V0; AFL-W2C8.9D
D2, D3: LED; LED_D5.0mm
H1, H2, H3, H4: MountingHole_4_40
IC1: LM2937ET-3.3_NOPB; TO254P470X1028X1955-3P; Mouser Part Number 926-LM2937ET-3.3NOPB
J1: JTAG; PinHeader_1x05_P2.54mm_Vertical
J2: Fan1; PinHeader_1x02_P2.54mm_Vertical
J3: Fans; PinHeader_1x02_P2.54mm_Vertical
J4: Logic; PinHeader_1x08_P2.54mm_Vertical
J5: On/Off; PinHeader_1x02_P2.54mm_Vertical
J6: Fan2; PinHeader_1x02_P2.54mm_Vertical
J8: USBC; PinHeader_1x08_P2.54mm_Vertical
J9: USBCFAN; PinHeader_1x08_P2.54mm_Vertical
Q1, Q2: IRLD024PBF; DIP920W60P254L490H457Q4N; Mouser Part Number 844-IRLD024PBF
R1: 1M; R_Axial_DIN0204_L3.6mm_D1.6mm_P7.62mm_Horizontal
R2, R3, R4, R7: 10k; R_Axial_DIN0204_L3.6mm_D1.6mm_P7.62mm_Horizontal
R5: 330; R_Axial_DIN0204_L3.6mm_D1.6mm_P7.62mm_Horizontal
R6: 820; R_Axial_DIN0204_L3.6mm_D1.6mm_P7.62mm_Horizontal
SW1: Reset; SW_PUSH_6mm
SW2: Mode; SW_PUSH_6mm
TP1: +5V; Testpoint_1x02_P2.54mm
TP2: GND; Testpoint_1x02_P2.54mm
TP3: +3.3V; Testpoint_1x02_P2.54mm
TP4: PF2; Testpoint_1x02_P2.54mm
U1: TM4C123GH6PMIR; QFP50P1200X1200X160-64N; Mouser Part Number 595-TM4C123GH6PMIR
U2: Adafruit ST7735R; adafruit_st7735r2
U4, U5, U7: HC-SR04; PinHeader_1x04_P2.54mm_Vertical
Y1: ABM3-16.000MHZ-B2-T; ABM3; Mouser Part Number 815-ABM3-16-B2-T

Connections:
+3V3: C3.1, C5.1, C6.1, C7.1, C11.1, C13.1, IC1.3 (OUTPUT), R1.1, R2.1, R6.2, TP3.1 (A), TP3.2 (B), U1.2 (VDDA), U1.11 (VDD_1), U1.26 (VDD_2), U1.37 (VBAT), U1.42 (VDD_3), U1.54 (VDD_4), U2.2 (VCC), U2.10 (LITE)
+5V: C12.1, C14.1, C15.1, C16.1, IC1.1 (INPUT), J5.1 (A), TP1.1 (A), TP1.2 (B), U4.1 (VCC), U5.1 (VCC), U7.1 (VCC)
+5V_MOTOR: D1.1 (K), D4.1 (K), J2.2 (B), J6.2 (B), J9.2
/LDO: C4.1, C8.1, C9.1, C10.1, U1.25 (VDDC_1), U1.56 (VDDC_2)
/OSC1: C1.1, U1.41 (OSC1), Y1.2
/OSC2: C2.1, U1.40 (OSC0), Y1.1
/Reset: R2.2, SW1.2, U1.38 (~RST)
/TCK: J1.2 (B), U1.52 (PC0/TCK/SWCLK)
/TDI: J1.4 (C), U1.50 (PC2/TDI)
/TDO: J1.5 (C), U1.49 (PC3/TDO/SWO)
/TMS: J1.3 (C), U1.51 (PC1/TMS/SWDIO)
GND: C1.2, C2.2, C3.2, C4.2, C5.2, C6.2, C7.2, C8.2, C9.2, C10.2, C11.2, C12.2, C13.2, C14.2, C15.2, C16.2, C17.2, D2.1 (K), D3.1 (K), IC1.2 (GND), J1.1 (A), J4.1, J8.1, SW1.1, SW2.1, TP2.1 (A), TP2.2 (B), U1.3 (GNDA), U1.12 (GND_1), U1.27 (GND_2), U1.34 (XOSC0), U1.35 (GNDX), U1.39 (GND_3), U1.55 (GND_4), U2.1 (GND), U4.4 (GND), U5.4 (GND), U7.4 (GND)
GND_MOTOR: J9.1, Q1.4 (S), Q2.4 (S)
unnamed: D1.2 (A), J6.1 (A), Q2.1 (D), Q2.2 (D)
unnamed: D2.2 (A), R5.1
unnamed: D3.2 (A), R6.1
unnamed: D4.2 (A), J2.1 (A), Q1.1 (D), Q1.2 (D)
unnamed: J5.2 (B), J8.2
unnamed: Q1.3 (G), R7.2
unnamed: Q2.3 (G), R3.2
unnamed: R4.2, SW2.2, TP4.1 (A), TP4.2 (B)
unnamed: R1.2, U1.32 (~WAKE)
PA0: U1.17 (PA0/U0RX)
PA1: U1.18 (PA1/U0TX)
PA2: U1.19 (PA2/SSI0C1K), U2.8 (SCK)
PA3: U1.20 (PA3/SSI0FSS), U2.6 (TFT_CS)
PA4: U1.21 (PA4/SSI0RX), U2.9 (MISO)
PA5: U1.22 (PA5/SSI0TX), U2.7 (MOSI)
PA6: U1.23 (PA6), U2.4 (D/C)
PA7: U1.24 (PA7), U2.3 (RESET)
PB0: U1.45 (PB0/USB0ID), U2.5 (CARD_CS)
PB1: U1.46 (PB1/USB0VBUS)
PB2: J4.3, U1.47 (PB2/I2C0SCL), U7.2 (TRIG)
PB3: J4.5, U1.48 (PB3/I2C0SDA), U5.2 (TRIG)
PB4: J4.7, U1.58 (PB4), U4.2 (TRIG)
PB5: J4.4, U1.57 (PB5), U7.3 (ECHO)
PB6: J4.6, U1.1 (PB6), U5.3 (ECHO)
PB7: J4.8, U1.4 (PB7), U4.3 (ECHO)
PC4: U1.16 (PC4)
PC5: U1.15 (PC5)
PC6: U1.14 (PC6)
PC7: U1.13 (PC7)
PD0: U1.61 (PD0)
PD1: U1.62 (PD1)
PD2: U1.63 (PD2)
PD3: U1.64 (PD3)
PD4: U1.43 (PD4)
PD5: U1.44 (PD5)
PD6: U1.53 (PD6)
PD7: U1.10 (PD7)
PE0: U1.9 (PE0)
PE1: U1.8 (PE1)
PE2: U1.7 (PE2)
PE3: U1.6 (PE3)
PE4: J3.1, R7.1, U1.59 (PE4)
PE5: J3.2, R3.1, U1.60 (PE5)
PF0: U1.28 (PF0)
PF1: J4.2, R5.2, U1.29 (PF1)
PF2: C17.1, R4.1, U1.30 (PF2)
PF3: U1.31 (PF3)
PF4: U1.5 (PF4)

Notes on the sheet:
Logic Analyzer Connections
Buttons (negative logic w/ internal pullup)
Motors/Fans
LEDs (Power and Heartbeat)
Ultrasonic Range Sensors
Display
Power Circuit
TM4C Chip
NOTE: used to be PB7 echo PB6 trig, and counting down for others
PF1 will be for general purpose debugging
Aidan, Alexa, Brian, Eric, Paul
NOTE: Using M0PWM4 (PE4) and M1PWM3 (PE5) (Page 1233 of datasheet)

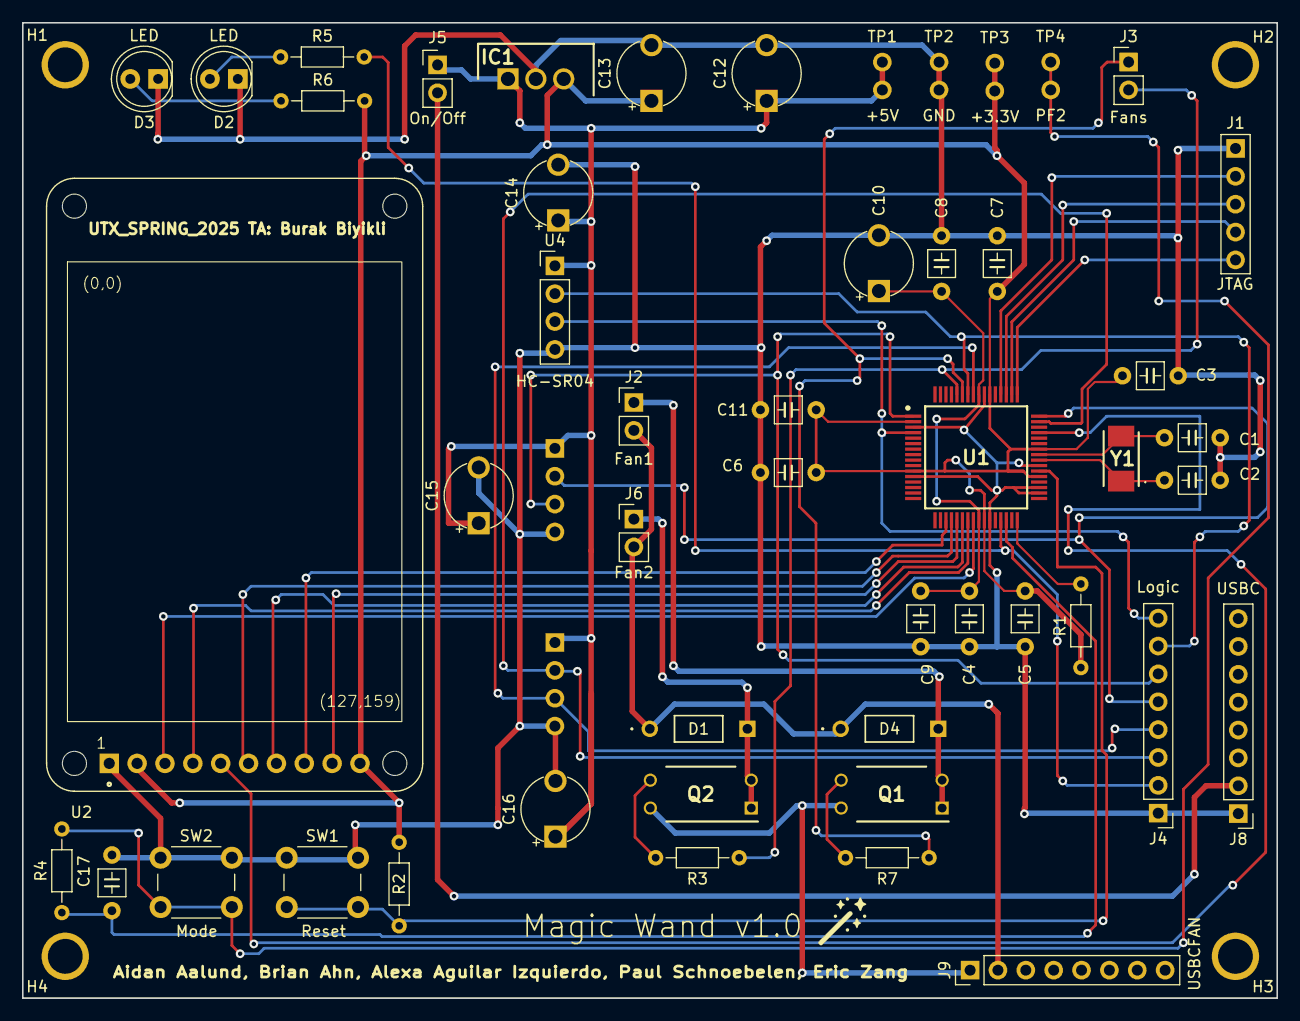
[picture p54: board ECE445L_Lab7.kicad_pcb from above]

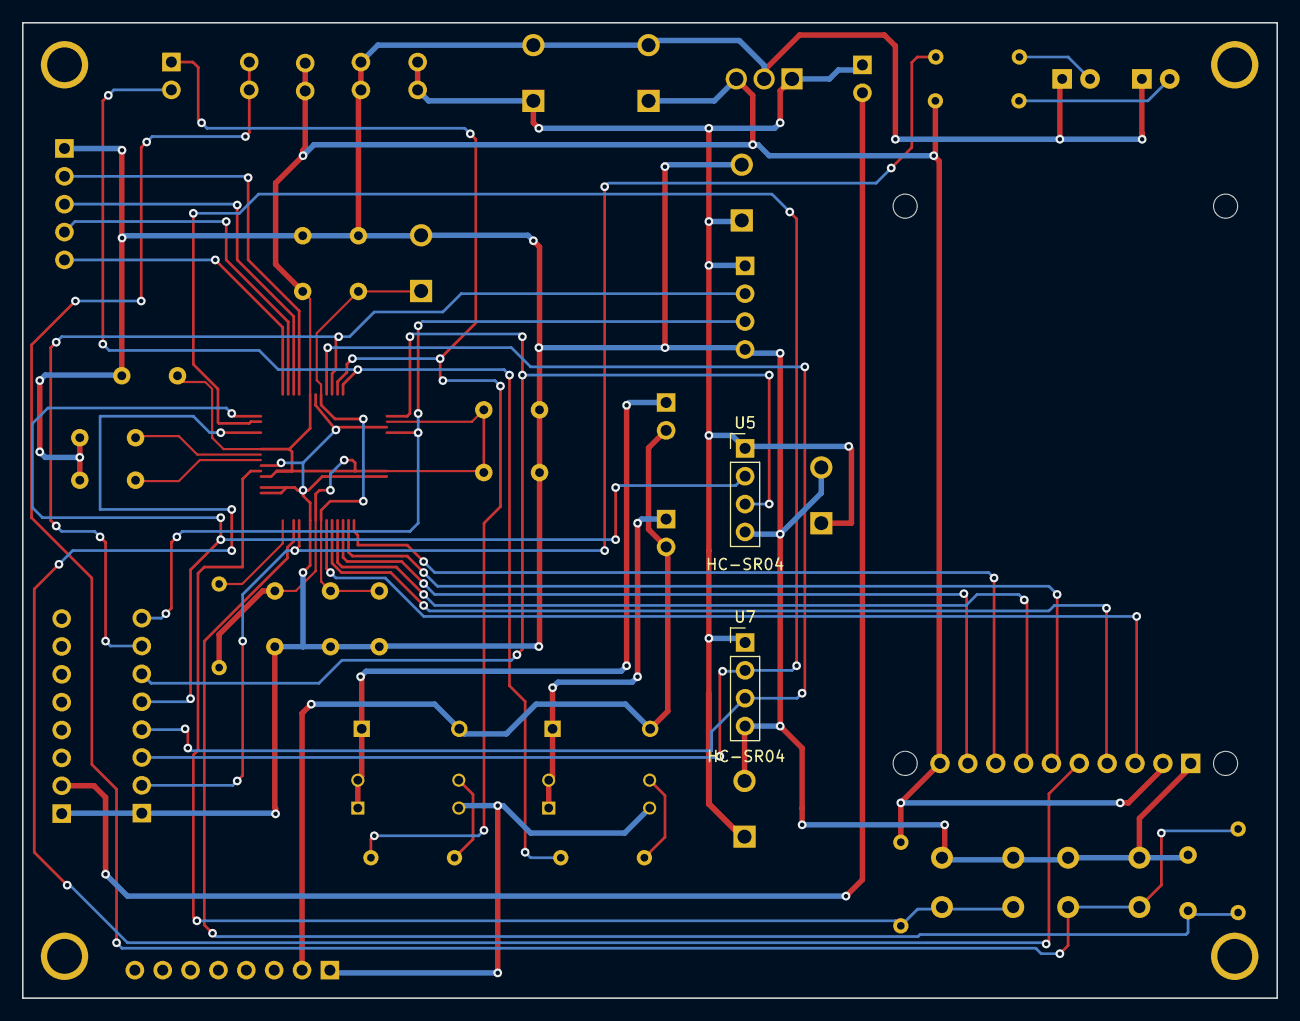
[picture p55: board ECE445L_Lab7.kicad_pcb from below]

Board: 2 copper layers, 114.4 x 88.9 mm, 55 parts (2 on the bottom side), 39 nets.

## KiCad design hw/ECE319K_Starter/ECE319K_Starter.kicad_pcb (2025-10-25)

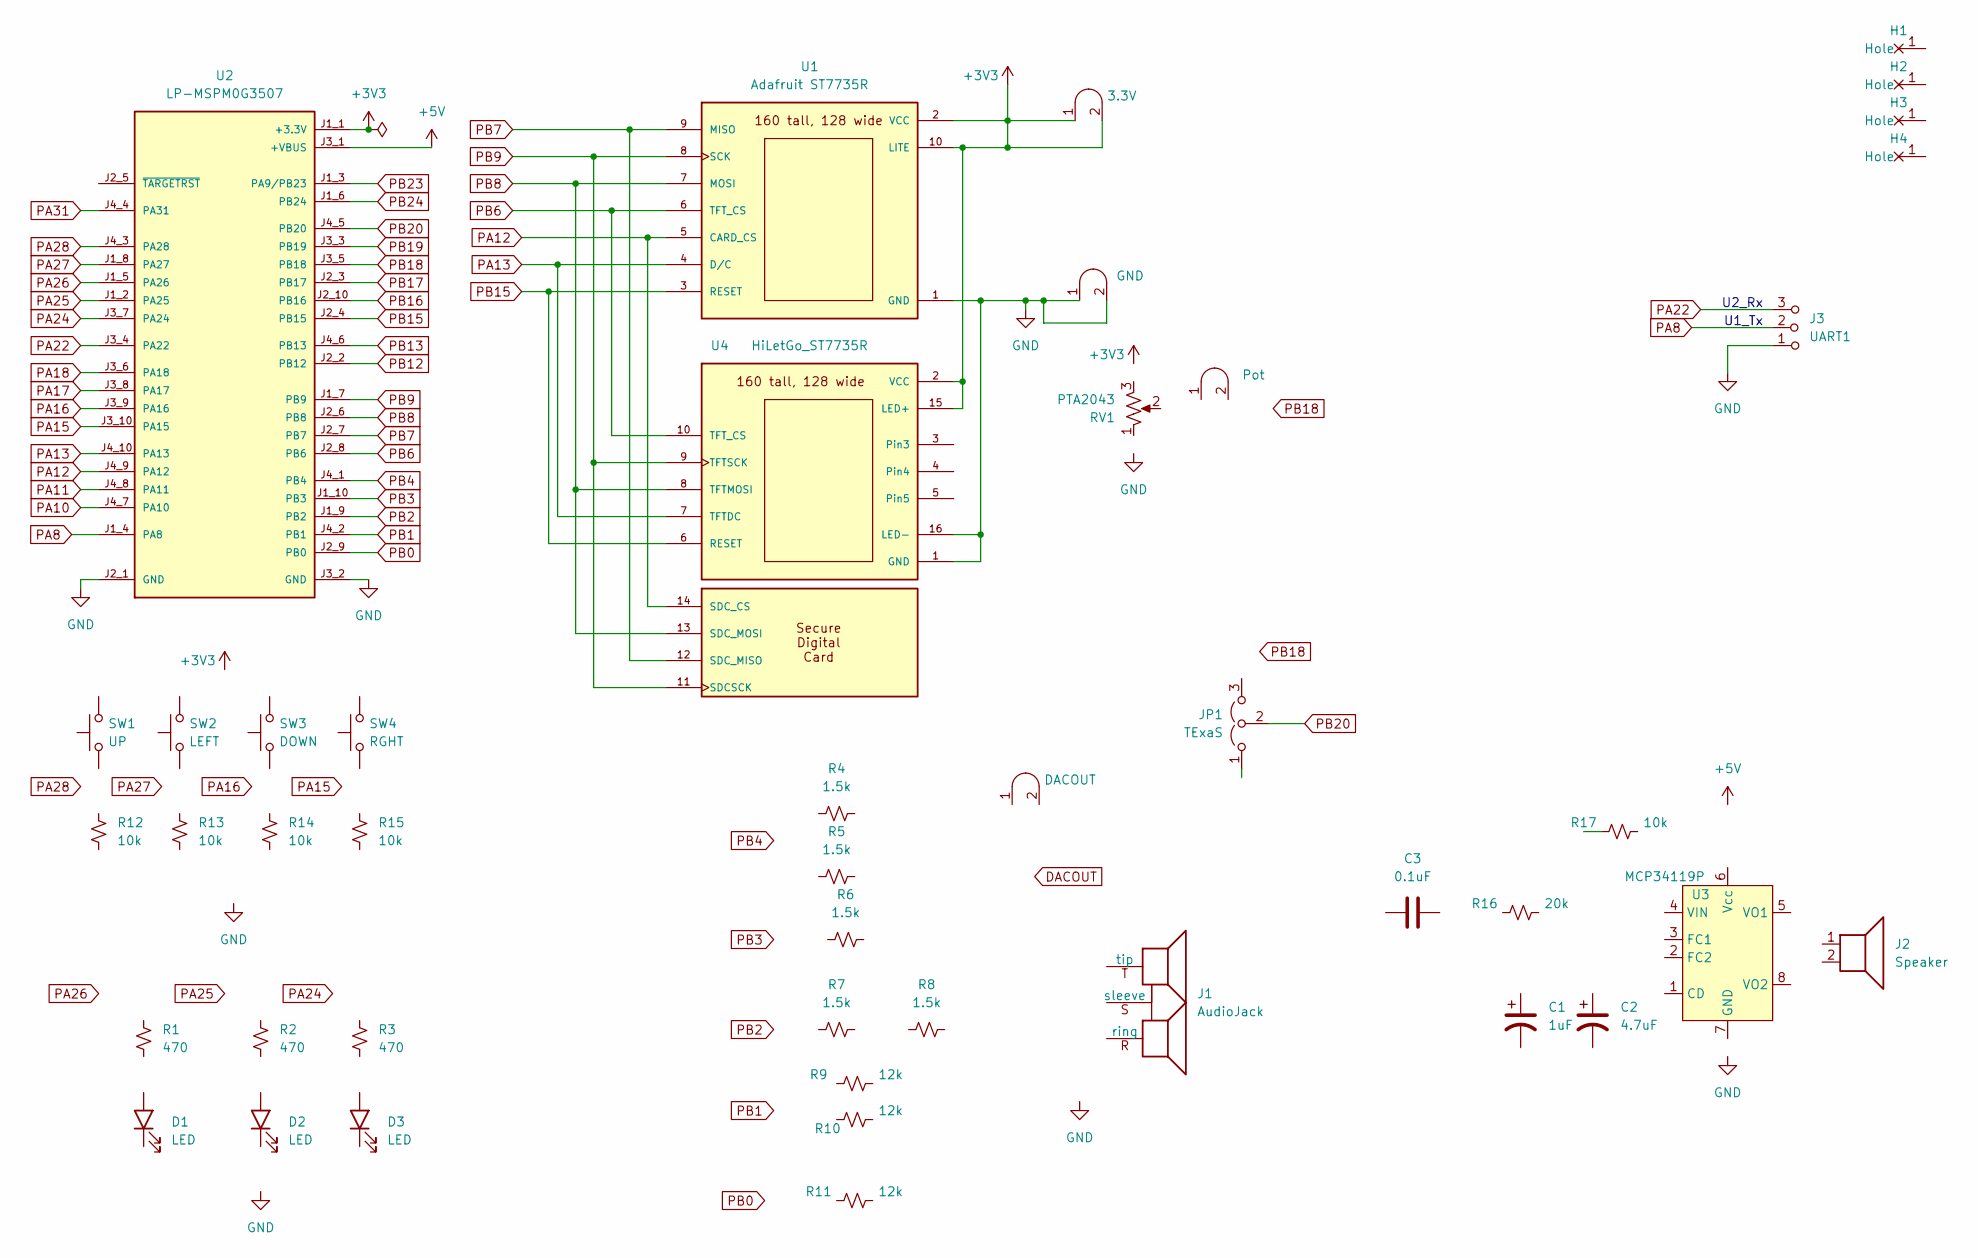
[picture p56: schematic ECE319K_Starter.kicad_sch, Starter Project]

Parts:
C1: 1uF; CP_Radial_Tantal200mil
C2: 4.7uF; CP_Radial_Tantal200mil
C3: 0.1uF; C_Axial_200mil
D1, D2, D3: LED; LED_D5.0mm
H1, H2, H3, H4: MountingHole_4_40
J1: AudioJack; Jack_3.5mm_CUI_SJ1-3523N_Horizontal
J2: Speaker; PinHeader_1x02_P2.54mm_Vertical
J3: UART1; PinHeader_1x03_P2.54mm_Vertical
J4: Pot; Testpoint_1x02_P2.54mm
J6: GND; Testpoint_1x02_P2.54mm
J7: DACOUT; Testpoint_1x02_P2.54mm
JP1: TExaS; PinHeader_1x03_P2.54mm_Vertical
R1, R2, R3: 470; R_Axial_DIN0204_L3.6mm_D1.6mm_P7.62mm_Horizontal
R4, R5, R6, R7, R8: 1.5k; R_Axial_DIN0204_L3.6mm_D1.6mm_P7.62mm_Horizontal
R9, R10, R11: 12k; R_Axial_DIN0204_L3.6mm_D1.6mm_P7.62mm_Horizontal
R12, R13, R14, R15, R17: 10k; R_Axial_DIN0204_L3.6mm_D1.6mm_P7.62mm_Horizontal
R16: 20k; R_Axial_DIN0204_L3.6mm_D1.6mm_P7.62mm_Horizontal
RV1: PTA2043; PTA2043pot
SW1: UP; SW_PUSH_6mm
SW2: LEFT; SW_PUSH_6mm
SW3: DOWN; SW_PUSH_6mm
SW4: RGHT; SW_PUSH_6mm
TP1: 3.3V; Testpoint_1x02_P2.54mm
U1: Adafruit ST7735R; adafruit_st7735r2
U2: LP-MSPM0G3507; ti_LP_MSPM0G3507
U3: MCP34119P; DIP-8_W7.62mm_LongPads
U4: HiLetGo_ST7735R; hiletgo_st7735r

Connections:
+3V3: TP1.1 (A), TP1.2 (B), U1.2 (VCC), U1.10 (LITE), U2.J1_1 (+3.3V), U4.2 (VCC), U4.15 (LED+)
+5V: U2.J3_1 (+VBUS)
GND: J3.1 (A), J6.1 (A), J6.2 (B), U1.1 (GND), U2.J2_1 (GND), U2.J3_2 (GND), U4.1 (GND), U4.16 (LED-)
PA8: J3.2 (B), U2.J1_4 (PA8)
PA10: U2.J4_7 (PA10)
PA11: U2.J4_8 (PA11)
PA12: U1.5 (CARD_CS), U2.J4_9 (PA12), U4.14 (SDC_CS)
PA13: U1.4 (D/C), U2.J4_10 (PA13), U4.7 (TFTDC)
PA15: U2.J3_10 (PA15)
PA16: U2.J3_9 (PA16)
PA17: U2.J3_8 (PA17)
PA18: U2.J3_6 (PA18)
PA22: J3.3 (C), U2.J3_4 (PA22)
PA24: U2.J3_7 (PA24)
PA25: U2.J1_2 (PA25)
PA26: U2.J1_5 (PA26)
PA27: U2.J1_8 (PA27)
PA28: U2.J4_3 (PA28)
PA31: U2.J4_4 (PA31)
PB0: U2.J2_9 (PB0)
PB1: U2.J4_2 (PB1)
PB2: U2.J1_9 (PB2)
PB3: U2.J1_10 (PB3)
PB4: U2.J4_1 (PB4)
PB6: U1.6 (TFT_CS), U2.J2_8 (PB6), U4.10 (TFT_CS)
PB7: U1.9 (MISO), U2.J2_7 (PB7), U4.12 (SDC_MISO)
PB8: U1.7 (MOSI), U2.J2_6 (PB8), U4.8 (TFTMOSI), U4.13 (SDC_MOSI)
PB9: U1.8 (SCK), U2.J1_7 (PB9), U4.9 (TFTSCK), U4.11 (SDCSCK)
PB12: U2.J2_2 (PB12)
PB13: U2.J4_6 (PB13)
PB15: U1.3 (RESET), U2.J2_4 (PB15), U4.6 (RESET)
PB16: U2.J2_10 (PB16)
PB17: U2.J2_3 (PB17)
PB18: U2.J3_5 (PB18)
PB19: U2.J3_3 (PB19)
PB20: JP1.2 (C), U2.J4_5 (PB20)
PB23: U2.J1_3 (PA9/PB23)
PB24: U2.J1_6 (PB24)

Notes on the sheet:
U2_Rx
U1_Tx

Board: 2 copper layers, 44 parts (1 on the bottom side), 12 nets, no tracks yet.

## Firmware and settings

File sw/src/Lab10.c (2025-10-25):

// Lab10.c
/*	
	Authors: Aidan Aalund, 
	Alexa Aguilar Izquierdo, Eric Zang, 
	Brian Ahn, Paul Schnoebelen
*/
// March 10th, 2025

// TODO: add includes
#include <stdint.h>
#include "../inc/tm4c123gh6pm.h"
#include "../inc/PLL.h"
#include "../inc/CortexM.h"
#include "../inc/LaunchPad.h"

#include "PulseWidthMeasure.h" // code for HC-SR40 sensor (could rename to DistanceSensor)
#include "Motor.h" // code for interfacing with the motor, PWM-ing a MOSFET (here for now, remove later)
#include "Display.h" // Adafruit display will show important info
#include "Buttons.h" // code for the mode switch button

// Globals
volatile uint8_t refreshFlag=0;


int main(){
	DisableInterrupts();
	
	// TODO: initialize drivers and devices here
	PLL_Init(Bus80MHz);     // 80 MHz clock
  LaunchPad_Init();       // activate port F
	Display_Init();
	//ButtonsInit();
	SensorSetup();
	MotorInit(); // Inits motors and control loop
	SysTick_Init_30kHz(); // 30Hz refresh rate
	
	
	EnableInterrupts();
	while(1){
		if (refreshFlag==1){
			refreshFlag=0;
			Draw_Refresh();
		}
	}
}

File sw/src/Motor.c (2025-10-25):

#include "Motor.h"
#include "PulseWidthMeasure.h"
#include <stdint.h>
#include "../inc/PLL.h"
#include "../inc/PWM.h"
#include "../inc/Timer1A.h"
#include "Buttons.h"

#define LENGTHFIXEDPOINT 60
#define MINPWM 10000
#define MAXPWM 59000
#define MAXHEIGHT 4

// Gains for tube 1 and tube 2 (OR MAYBE REGIONS OF THE TUBE)
static int32_t Kp1 = 1024;//2048
static int32_t Kp2 = 1;//1
static int32_t Ki1 = 1;//1
static int32_t Ki2 = 2;//2

static int32_t DesiredPosition = 0;
static int32_t LeftPosition = 0;
static int32_t RightPosition = 0;
static int32_t LeftU = 0;
static int32_t RightU = 0;
static int32_t LeftE = 0;
static int32_t RightE = 0;

static int32_t LeftBuf[100] = {0};
static int32_t RightBuf[100] = {0};
static int32_t AveLeftE = 0;
static int32_t LeftSum = 0;
static int32_t AveRightE = 0;
static int32_t RightSum = 0;

//Distance from sensor in cm
uint32_t oscillatingDistance [512] = {
30, 30, 30, 31, 31, 31, 31, 32, 32, 32, 32, 33, 33, 33, 33, 34,
34, 34, 34, 35, 35, 35, 35, 36, 36, 36, 36, 37, 37, 37, 37, 37,
38, 38, 38, 38, 39, 39, 39, 39, 39, 40, 40, 40, 40, 40, 41, 41,
41, 41, 42, 42, 42, 42, 42, 42, 43, 43, 43, 43, 43, 44, 44, 44,
44, 44, 44, 45, 45, 45, 45, 45, 45, 46, 46, 46, 46, 46, 46, 46,
47, 47, 47, 47, 47, 47, 47, 48, 48, 48, 48, 48, 48, 48, 48, 48,
48, 49, 49, 49, 49, 49, 49, 49, 49, 49, 49, 49, 49, 49, 50, 50,
50, 50, 50, 50, 50, 50, 50, 50, 50, 50, 50, 50, 50, 50, 50, 50,
50, 50, 50, 50, 50, 50, 50, 50, 50, 50, 50, 50, 50, 50, 50, 50,
50, 50, 50, 49, 49, 49, 49, 49, 49, 49, 49, 49, 49, 49, 49, 49,
48, 48, 48, 48, 48, 48, 48, 48, 48, 48, 47, 47, 47, 47, 47, 47,
47, 46, 46, 46, 46, 46, 46, 46, 45, 45, 45, 45, 45, 45, 44, 44,
44, 44, 44, 44, 43, 43, 43, 43, 43, 42, 42, 42, 42, 42, 42, 41,
41, 41, 41, 40, 40, 40, 40, 40, 39, 39, 39, 39, 39, 38, 38, 38,
38, 37, 37, 37, 37, 37, 36, 36, 36, 36, 35, 35, 35, 35, 34, 34,
34, 34, 33, 33, 33, 33, 32, 32, 32, 32, 31, 31, 31, 31, 30, 30,
30, 30, 30, 29, 29, 29, 29, 28, 28, 28, 28, 27, 27, 27, 27, 26,
26, 26, 26, 25, 25, 25, 25, 24, 24, 24, 24, 23, 23, 23, 23, 23,
22, 22, 22, 22, 21, 21, 21, 21, 21, 20, 20, 20, 20, 20, 19, 19,
19, 19, 18, 18, 18, 18, 18, 18, 17, 17, 17, 17, 17, 16, 16, 16,
16, 16, 16, 15, 15, 15, 15, 15, 15, 14, 14, 14, 14, 14, 14, 14,
13, 13, 13, 13, 13, 13, 13, 12, 12, 12, 12, 12, 12, 12, 12, 12,
12, 11, 11, 11, 11, 11, 11, 11, 11, 11, 11, 11, 11, 11, 10, 10,
10, 10, 10, 10, 10, 10, 10, 10, 10, 10, 10, 10, 10, 10, 10, 10,
10, 10, 10, 10, 10, 10, 10, 10, 10, 10, 10, 10, 10, 10, 10, 10,
10, 10, 10, 11, 11, 11, 11, 11, 11, 11, 11, 11, 11, 11, 11, 11,
12, 12, 12, 12, 12, 12, 12, 12, 12, 12, 13, 13, 13, 13, 13, 13,
13, 14, 14, 14, 14, 14, 14, 14, 15, 15, 15, 15, 15, 15, 16, 16,
16, 16, 16, 16, 17, 17, 17, 17, 17, 18, 18, 18, 18, 18, 18, 19,
19, 19, 19, 20, 20, 20, 20, 20, 21, 21, 21, 21, 21, 22, 22, 22,
22, 23, 23, 23, 23, 23, 24, 24, 24, 24, 25, 25, 25, 25, 26, 26,
26, 26, 27, 27, 27, 27, 28, 28, 28, 28, 29, 29, 29, 29, 30, 30
};

uint32_t hover = 40;
uint32_t oscillation = 31;
uint32_t tubeMode = 1;

void MotorInit(){
	PWM0E_Init(60000,50000); // 667hz, 75% duty on PE4 fan1 left
	PWM0F_Init(60000,50000); // 667hz, 75% duty on PE5 fan2 right
	Timer1A_Init(&PIControlLoop,5000000,2); // samplingTime = 0.0625 is 2500000, half that is 1250000, 
}

//int bu = 0; //TO DELETE

void PIControlLoop(void){
	
	//Test Burak
//	int be = 9000 - GetRightPosition(); //10 to 120,000
//	int bp = (be * Kp1)/Kp2;
//	bu += (be * Ki1)/Ki2;
//	bu = bu < MINPWM ? MINPWM : bu;
//	bu = bu > MAXPWM ? MAXPWM : bu;
//	int bt = bp + bu;
//	bt = bt < MINPWM ? MINPWM : bt;
//	bt = bt > MAXPWM ? MAXPWM : bt;
//	PWM0F_Duty(bt);
//	return;
	//End Test Burak

	//tubeMode = getMode();
	//tubeMode = 1; // debug
	tubeMode = 2; // debug
	
	int32_t oldLeft = LeftPosition;
	int32_t oldRight = RightPosition;
	int32_t oldDesired = DesiredPosition;
	
	LeftPosition = ((((int32_t)GetLeftPosition() / 2320)*3) + oldLeft) / 4;
	RightPosition = ((((int32_t)GetRightPosition() / 2320)*3) + oldRight) / 4;
	//LeftPosition = (int32_t)GetLeftPosition() / 2320;
	//RightPosition = (int32_t)GetRightPosition() / 2320;
	
	if(LeftPosition > 60){LeftPosition = 60;}
	if(RightPosition > 60){RightPosition = 60;}
	
	// Determine ERROR
	//Mode0 -> oscillating seperately
	if (tubeMode == 0) { // TODO: oscillating mode is just a underdamped set of gains...
		//LeftE = (int32_t)() - (int32_t)(LENGTHFIXEDPOINT-LeftPosition);
		RightE = (int32_t)(oscillatingDistance[oscillation%512]) - (int32_t)(LENGTHFIXEDPOINT-RightPosition);
	} else if ( tubeMode ==1){
		LeftE = (int32_t)(hover) - (int32_t)(LENGTHFIXEDPOINT-LeftPosition);
		RightE = (int32_t)(hover) - (int32_t)(LENGTHFIXEDPOINT-RightPosition);
			
	} else {
		DesiredPosition = ((((int32_t)GetDesiredPosition() / 2320)*3) + oldDesired) / 4;
		if(DesiredPosition > 55){DesiredPosition = 55;}
		LeftE = (int32_t)(DesiredPosition) - (int32_t)(LENGTHFIXEDPOINT-LeftPosition);
		RightE = (int32_t)(DesiredPosition) - (int32_t)(LENGTHFIXEDPOINT-RightPosition);
	}

	// Proportional terms
	int32_t P1 = (Kp1*LeftE)/Kp2;
	int32_t P2 = (Kp1*RightE)/Kp2;

	if(P1 < -10000) P1 = -10000;         // Minimum P
	if(P1 > MAXPWM) P1 = MAXPWM;       
	if(P2 < -10000) P2 = -10000;         // Minimum P
	if(P2 >MAXPWM) P2 = MAXPWM;       

	// Integral terms from SUM(KiDt)   
	static int32_t I1 =  0;
	static int32_t I2 = 0;

	// sliding window average
	static int32_t idx = 0;

	// Remove oldest value
	LeftSum -= LeftBuf[idx];
	RightSum -= RightBuf[idx];

	// Add new value
	LeftBuf[idx] = LeftE;
	RightBuf[idx] = RightE;
	LeftSum += LeftE;
	RightSum += RightE;

	idx = (idx+1)%100;

	AveLeftE = LeftSum/100; 
	AveRightE = RightSum/100;

	I1 = I1 + (Ki1*LeftE)/Ki2;
	I2 = I2 + (Ki1*RightE)/Ki2;      
	
	if(I1 > MAXPWM){I1 = MAXPWM;} // TODO: retune these
	if(I1 < -4000){I1 = -4000;}
	if(I2 > MAXPWM){I2 = MAXPWM;}
	if(I2 < -4000){I2 = -4000;}
	
	LeftU = P1 + I1;
	RightU = P2 + I2;

	// TODO: tune these to avoid crashing or falling down fast.
	
	if(LeftU < MINPWM)  LeftU= MINPWM;           // Minimum PWM output
	if(LeftU > MAXPWM) LeftU= MAXPWM;         
	if(RightU < MINPWM)  RightU= MINPWM;           // Minimum PWM output
	if(RightU > MAXPWM) RightU= MAXPWM;         
	
	// TODO: check for ball too close to sensors, if so, turn off to avoid damaging the sensor.
	if(LeftPosition < 8){
		PWM0E_Duty(2*MINPWM);
	} else {
		PWM0E_Duty(LeftU);
	}
	
	if(RightPosition < 5){
		PWM0F_Duty(2*MINPWM);
	} else {
		PWM0F_Duty(RightU);
	}
	
}

int mainMotor(){
	PLL_Init(Bus80MHz);	// bus clock at 80 MHz

  while(1){
		
  }
}

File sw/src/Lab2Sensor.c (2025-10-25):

// Lab2Sensor.c

#include "Lab2Sensor.h"
#include <stdint.h>
#include "../inc/tm4c123gh6pm.h"
#include "../inc/PLL.h"
#include "../inc/CortexM.h"
#include "../inc/LaunchPad.h"

void ADC_Init(void){
  SYSCTL_RCGCADC_R |= 0x0001;   // 1) activate ADC0
  SYSCTL_RCGCGPIO_R |= 0x10;    // 2) activate clock for Port E
  while((SYSCTL_PRGPIO_R&0x10) != 0x10){};  // 3 for stabilization
  GPIO_PORTE_DIR_R &= ~0x20;    // 4) make PE5 input
  GPIO_PORTE_AFSEL_R |= 0x20;   // 5) enable alternate function on PE5
  GPIO_PORTE_DEN_R &= ~0x20;    // 6) disable digital I/O on PE5
  GPIO_PORTE_AMSEL_R |= 0x20;   // 7) enable analog functionality on PE5
  while((SYSCTL_PRADC_R&0x0001) != 0x0001){}; // good code, but not implemented in simulator
  ADC0_PC_R &= ~0xF;
  ADC0_PC_R |= 0x1;             // 8) configure for 125K samples/sec
  ADC0_SSPRI_R = 0x0123;        // 9) Sequencer 3 is highest priority
  ADC0_ACTSS_R &= ~0x0008;      // 10) disable sample sequencer 3
  ADC0_EMUX_R &= ~0xF000;       // 11) seq3 is software trigger
  ADC0_SSMUX3_R &= ~0x000F;
  ADC0_SSMUX3_R += 8;           // 12) set channel 8 (PE5's channel)
  ADC0_SSCTL3_R = 0x0006;       // 13) no TS0 D0, yes IE0 END0
  ADC0_IM_R &= ~0x0008;         // 14) disable SS3 interrupts
  ADC0_ACTSS_R |= 0x0008;       // 15) enable sample sequencer 3
}
// Aidan: Code modified from book
int32_t ADC_In(void){
  uint32_t result;
  ADC0_PSSI_R = 0x0008;            // 1) initiate SS3
  while((ADC0_RIS_R&0x08)==0){};   // 2) wait for conversion done
  result = ADC0_SSFIFO3_R&0xFFF;   // 3) read result
  ADC0_ISC_R = 0x0008;             // 4) acknowledge completion
  return result;
}

#define A 99159
#define B -507
#define IRmax 900
#define Dmax 400
int32_t IR_Convert(int32_t n){  // returns distance in mm
	int32_t dist = A/(n+B);
	return dist;
}

// Unit test main
void main1(){
	PLL_Init(Bus80MHz);     // 80 MHz clock
  LaunchPad_Init();       // activate port F
  ADC_Init();
 
	while(1){
    uint32_t d = IR_Convert(ADC_In());
		//Clock_Delay1ms(1000); // TODO: uncommenting this doesn't compile
  }
	
}
